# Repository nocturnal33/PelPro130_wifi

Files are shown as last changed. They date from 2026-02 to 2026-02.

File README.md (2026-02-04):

> [!CAUTION]
> ADD AT YOUR OWN RISK! <br>
> THIS CONTROLS FIRE IN YOUR HOUSE!<br>
> IF YOU ARE NOT COMFORTABLE WITH ANY OF THIS, WALK AWAY
> I AM NOT RESPONSIBEL FOR ANY DAMAGE TO YOUR PELLET STOVE OR HOUSE.

# Add wifi to your PelPro 130
*This has only been tested on a PelPro 130*

## YOU WILL NEED TO TEST THIS BEFORE RUNNING UNATTENDED
I have had this running for months with no issues. Again, If you don't feel comfortable messing with the controls of you pellet stove - **DON'T DO IT!**

## Purpose
The purpose of this is to be able to turn on the pellet stove from anywhere in the house. Maybe it's 2am and it's getting cold in the house. Go to the IP address, login, and turn it on. You cann turn it off, adjust heat level, all from the comfort of your bed.<br>
You still have to make sure you have Pellets loaded, the burn pot is clean, etc... <br>
This project assumes you are at home, near the PelPro if something were to go wrong - you will be there to monitor the pellet stove.

## Parts: 
- EMAX Servo ES08A (x1)
- ELEGOO ESP-32 (Or similar) (x1)
- 8mm x 2mm Round Magnets (x3)
- M2 X4 Hex screws (x5)
   - For Servo (x2)
   - For ESP32 (x3)

## 3D print the parts in ABS, PETG, or ASA. Do not use PLA
- Servo Motor / ESP case
- Servo Spur gear
- PelPro Gear

## Flash ESP32
- Use your IP Address / Subnet / DNS
- Create your password or omit it if needed

## Solder or connect servo wires to ESP32
- SERVO  -  RED    -  3.3v
- SERVO  -  BROWN  -  Ground
- SERVO  -  ORANGE -  GPIO18

After 3D printing parts - super glue magnets in enclosure, screw in the ESP32 using M2 screws, screw in the Servo using M2 screws.

1. Remove the knob on the PelPro 130 and replace with printed gear. Use a little sticky tack to make sure it does not come off.
2. Attach the magnetic base to the pellet stove
3. Attach the spur gear to the servo
4. Align the gears
5. With the Pellet stove OFF, go to the IP Address and test the alignment
6. Go to the IP address you selected in the .ino file and enter the password you chose
7. Test
8. Turn ON the pellet stove and enjoy

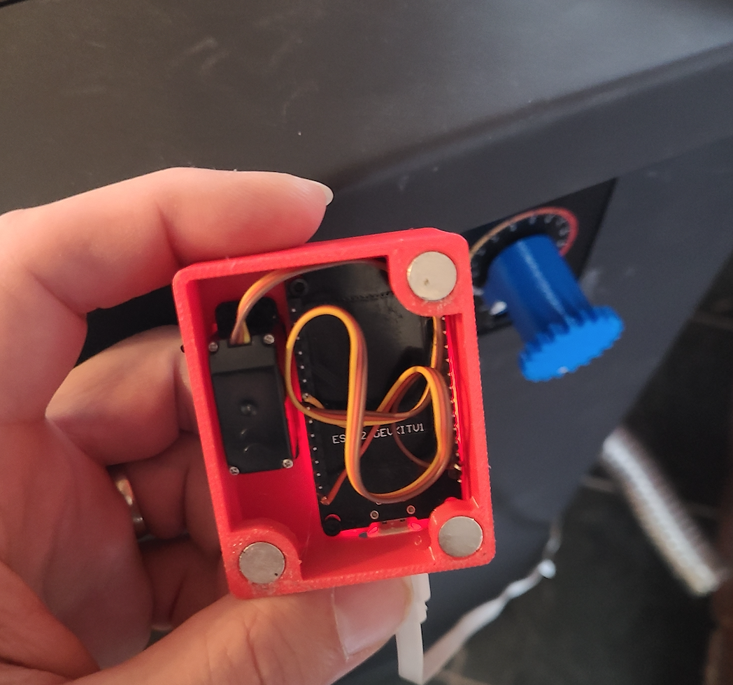
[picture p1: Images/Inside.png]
Inside of enclosure

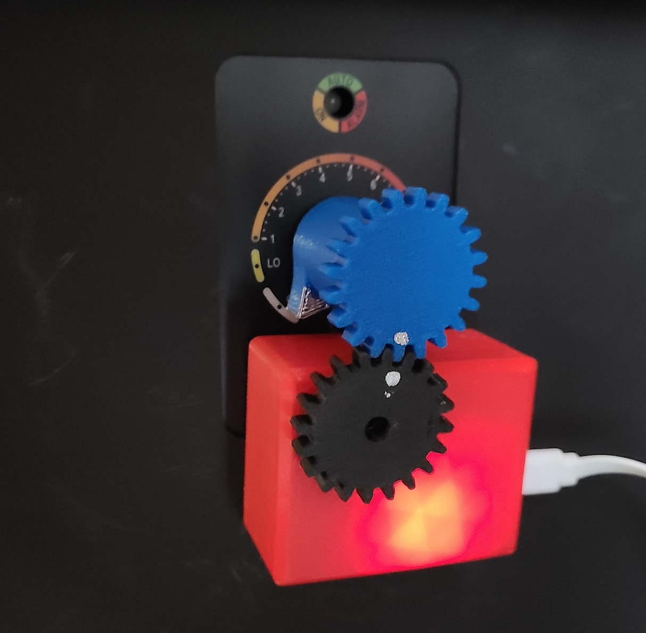
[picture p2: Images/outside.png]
Front of enclosure


## Manually adjusting heat on the PP130
Now that the servo is attached to the pellet stove, it will be harder to manually turn on the pellet stove. Keep an old phone or tablet near the PelPro 130 and use that instead of manually adjusting, or, because it is magnetically attached, move it away from the spur gear and adjust.

## Home Assistant.
This works great with Home Assistant. I am using my Google Nest to check the inside temperature and turn on the Pellet Stove based on the min and turn off on the max. Lots of ways to do this, but this works for my setup.  
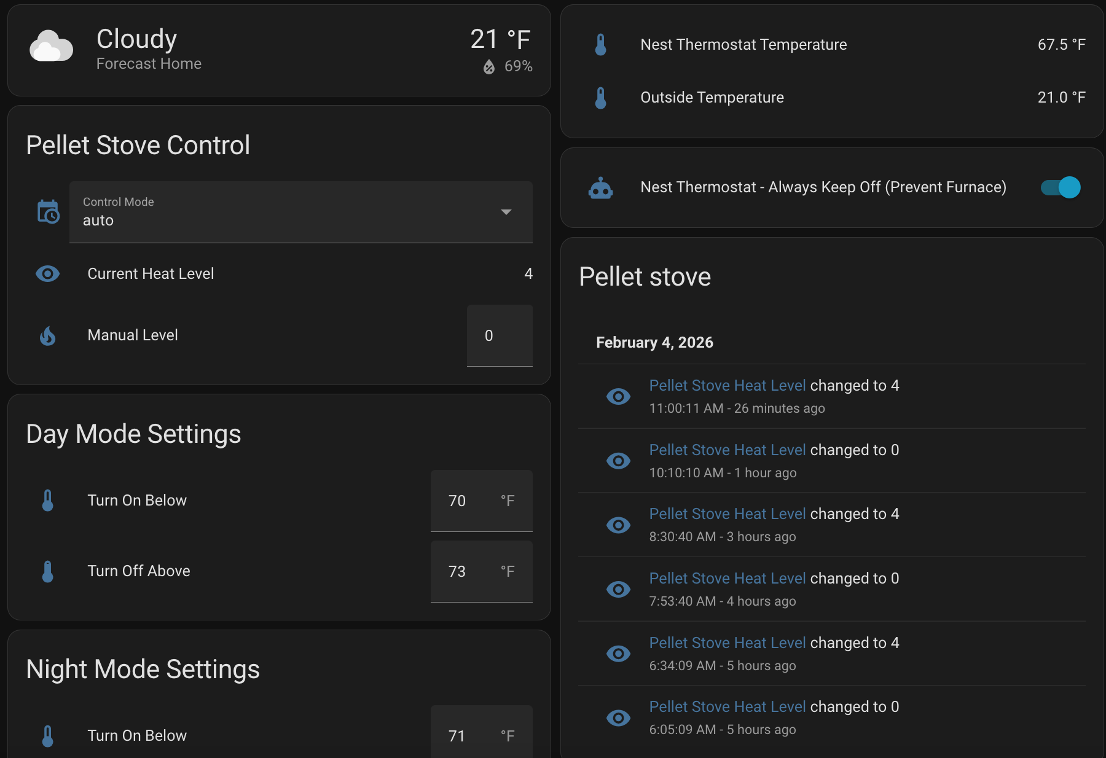
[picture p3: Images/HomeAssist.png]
Home Assistant


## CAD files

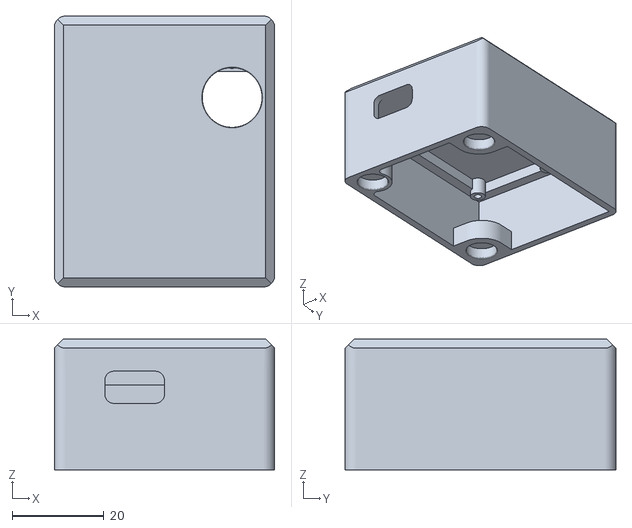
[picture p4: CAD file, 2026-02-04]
3D-Models/PelPro-Wifi-Enclosure.stl
48.0 x 59.0 x 28.5

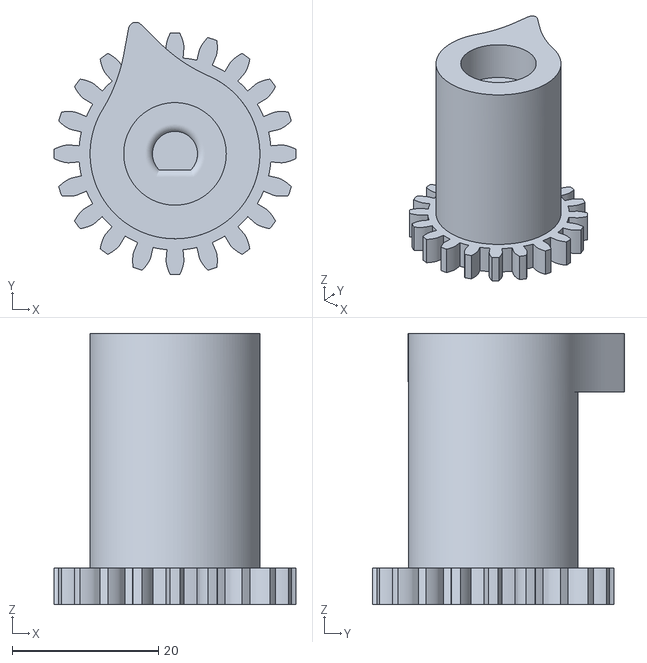
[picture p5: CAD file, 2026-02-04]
3D-Models/PelPro130-SpurGear.stl
33.0 x 34.5 x 37.0

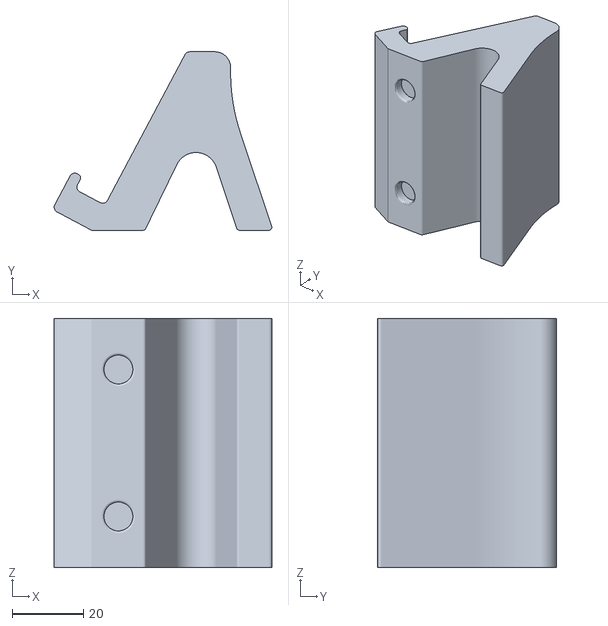
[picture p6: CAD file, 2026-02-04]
3D-Models/PhoneStand.stl
61.2 x 50.2 x 70.0

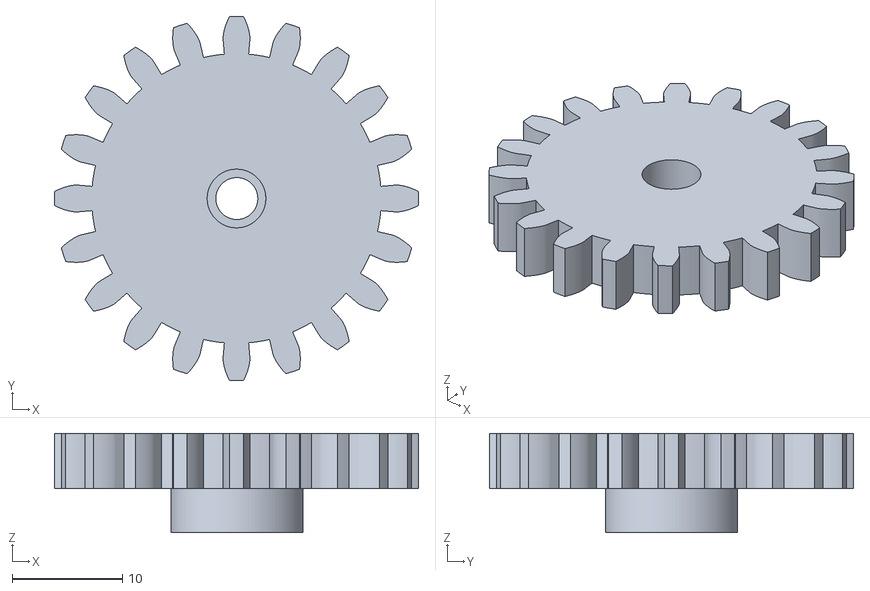
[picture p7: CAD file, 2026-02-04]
3D-Models/ServoSpurGear.stl
33.0 x 33.0 x 9.00

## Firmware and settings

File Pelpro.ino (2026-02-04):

#include <WiFi.h>
#include <WebServer.h>
#include <ESP32Servo.h>

// WiFi credentials
const char* ssid = "";
const char* password = "";

// Static IP configuration
// (Make sure to fill these in with your specific network details)
IPAddress local_IP(192, 168, 1, 200); // Change this IP to a static IP on your network
IPAddress gateway(192, 168, 1, 1);    // Use your Local IP gateway - or leave blank to keep on LAN mode
IPAddress subnet(255, 255, 255, 0);
IPAddress primaryDNS(8, 8, 8, 8);  
IPAddress secondaryDNS(8, 8, 4, 4);

// Servo setup
Servo myServo;
const int servoPin = 18;

// LED setup
const int ledPin = 2; // Built-in LED on GPIO2
unsigned long lastLedBlink = 0;
bool ledState = false;

// Web server on port 80
WebServer server(80);

// Current Heat level (0-8)
int HeatLevel = 0;

// Control LED and Servo based on WiFi status
void updateWiFiLED() {
  static wl_status_t lastWifiStatus = WL_IDLE_STATUS;
  wl_status_t wifiStatus = WiFi.status();
  unsigned long currentTime = millis();
  
  // Check if WiFi was just disconnected
  if (lastWifiStatus == WL_CONNECTED && wifiStatus != WL_CONNECTED) {
    // WiFi just disconnected
    // REMOVED: myServo.write(0) and HeatLevel = 0
    Serial.println("WiFi disconnected - Maintaining current Heat Level");
  }
  
  lastWifiStatus = wifiStatus;
  
  switch (wifiStatus) {
    case WL_CONNECTED:
      // Solid LED when connected (active-low LED usually, usually LOW is ON for built-in)
      // If your LED is off when connected, swap LOW/HIGH here
      digitalWrite(ledPin, LOW); 
      break;
      
    case WL_IDLE_STATUS:
    case WL_NO_SSID_AVAIL:
    case WL_SCAN_COMPLETED:
    case WL_CONNECT_FAILED:
    case WL_CONNECTION_LOST:
    case WL_DISCONNECTED:
      // Fast blink when disconnected or failed (250ms intervals)
      if (currentTime - lastLedBlink >= 250) {
        ledState = !ledState;
        digitalWrite(ledPin, ledState ? HIGH : LOW);
        lastLedBlink = currentTime;
      }
      break;
      
    default:
      // Slow blink for any other status (1 second intervals)
      if (currentTime - lastLedBlink >= 1000) {
        ledState = !ledState;
        digitalWrite(ledPin, ledState ? HIGH : LOW);
        lastLedBlink = currentTime;
      }
      break;
  }
}

// Main control page HTML (no password protection)
const char webpage[] PROGMEM = R"=====(
<!DOCTYPE html>
<html>
<head>
  <meta charset="UTF-8">
  <meta name="viewport" content="width=device-width, initial-scale=1">
  <title>Heat Control</title>
  <style>
    body {
      font-family: Arial, sans-serif;
      text-align: center;
      margin-top: 50px;
      background-color: #f0f0f0;
    }
    h1 {
      color: #333;
      font-size: 30px;
      font-weight: bold;
      margin-bottom: 20px;
    }
    .slider-container {
      margin: 30px auto;
      width: 80%;
      max-width: 500px;
    }
    .slider {
      width: 100%;
      height: 75px;
      background: #f0f0f0;
      outline: none;
      opacity: 0.7;
      transition: opacity 0.2s;
      cursor: pointer;
      -webkit-appearance: none;
      appearance: none;
      border-radius: 10px;
    }
    
    .slider::-webkit-slider-thumb {
      -webkit-appearance: none;
      appearance: none;
      width: 30px;
      height: 30px;
      background: #fff;
      cursor: pointer;
      border-radius: 50%;
      border: 3px solid #f44336;
      box-shadow: 0 2px 6px rgba(0,0,0,0.3);
    }
    
    .slider::-moz-range-thumb {
      width: 30px;
      height: 30px;
      background: #fff;
      cursor: pointer;
      border-radius: 50%;
      border: 3px solid #f44336;
      box-shadow: 0 2px 6px rgba(0,0,0,0.3);
    }
    
    .slider::-webkit-slider-track {
      height: 20px;
      background: #f44336;
      border-radius: 10px;
      border: none;
    }
    
    .slider::-webkit-slider-runnable-track {
      height: 20px;
      background: #f44336;
      border-radius: 10px;
      border: none;
    }
    
    .slider::-moz-range-track {
      height: 20px;
      background: #f44336;
      border-radius: 10px;
      border: none;
    }
    
    .slider:hover {
      opacity: 1;
    }
    .value-display {
      font-size: 48px;
      font-weight: bold;
      color: #4CAF50;
      margin: 20px;
    }
    .labels {
      display: flex;
      justify-content: space-between;
      margin-top: 20px;
      font-size: 14px;
      color: #666;
    }
    
    .labels span {
      cursor: pointer;
      padding: 5px 10px;
      border-radius: 3px;
      transition: background-color 0.2s;
    }
    
    .labels span:hover {
      background-color: rgba(244, 67, 54, 0.1);
    }
  </style>
</head>
<body>
  <h1>PelPro 130 - Heat Control</h1>
  <div class="value-display" id="HeatDisplay">0</div>
  <div class="slider-container">
    <input type="range" min="0" max="8" value="0" class="slider" id="HeatSlider">
    <div class="labels">
      <span onclick="setHeat(0)">OFF</span>
      <span onclick="setHeat(1)">1</span>
      <span onclick="setHeat(2)">2</span>
      <span onclick="setHeat(3)">3</span>
      <span onclick="setHeat(4)">4</span>
      <span onclick="setHeat(5)">5</span>
      <span onclick="setHeat(6)">6</span>
      <span onclick="setHeat(7)">7</span>
      <span onclick="setHeat(8)">8</span>
    </div>
  </div>

  <script>
    var slider = document.getElementById("HeatSlider");
    var display = document.getElementById("HeatDisplay");
    var isDragging = false; 

    slider.onmousedown = function() { isDragging = true; }
    slider.onmouseup = function() { isDragging = false; }
    slider.ontouchstart = function() { isDragging = true; }
    slider.ontouchend = function() { isDragging = false; }
    
    // Set Heat when clicking on labels
    function setHeat(level) {
      slider.value = level;
      display.innerHTML = level;
      
      var xhr = new XMLHttpRequest();
      xhr.open("GET", "/setHeat?level=" + level, true);
      xhr.send();
    }
    
    slider.oninput = function() {
      display.innerHTML = this.value;
    }
    
    slider.onchange = function() {
      var xhr = new XMLHttpRequest();
      xhr.open("GET", "/setHeat?level=" + this.value, true);
      xhr.send();
      isDragging = false;
    }

    function getHeatState() {
      // Only refresh if the user isn't actively dragging
      if (isDragging) {
        return;
      }
      
      var xhr = new XMLHttpRequest();
      xhr.onreadystatechange = function() {
        if (this.readyState == 4 && this.status == 200) {
          slider.value = this.responseText;
          display.innerHTML = this.responseText;
        }
      };
      xhr.open("GET", "/getHeat", true);
      xhr.send();
    }
    
    window.onload = getHeatState;
    setInterval(getHeatState, 10000); // 10000ms = 10 seconds
  </script>
</body>
</html>
)=====";

void handleRoot() {
  server.send(200, "text/html", webpage);
}

void handleSetHeat() {
  if (server.hasArg("level")) {
    HeatLevel = server.arg("level").toInt();
    HeatLevel = constrain(HeatLevel, 0, 8);
    
    int servoAngle = map(HeatLevel, 0, 8, 0, 180);
    myServo.write(servoAngle);
    
    Serial.print("Heat set to: ");
    Serial.print(HeatLevel);
    Serial.print(" | Servo angle: ");
    Serial.println(servoAngle);
    
    server.send(200, "text/plain", "OK");
  } else {
    server.send(400, "text/plain", "Bad Request");
  }
}

void handleGetHeat() {
  server.send(200, "text/plain", String(HeatLevel));
}

void setup() {
  Serial.begin(115200);
  
  // Initialize servo
  myServo.attach(servoPin);
  myServo.write(0); // Start at 0 on POWER UP only
  
  // Initialize LED (active-low)
  pinMode(ledPin, OUTPUT);
  digitalWrite(ledPin, HIGH); // Start with LED off (active-low)
  
  // Configure static IP
  // IMPORTANT: Ensure your specific IP addresses are entered here
  if (!WiFi.config(local_IP, gateway, subnet, primaryDNS, secondaryDNS)) {
    Serial.println("Static IP configuration failed!");
  }
  
  // Connect to WiFi
  Serial.println();
  Serial.print("Connecting to ");
  Serial.println(ssid);
  
  WiFi.begin(ssid, password);
  
  // Loop to wait for connection
  while (WiFi.status() != WL_CONNECTED) {
    delay(500);
    Serial.print(".");
  }
  
  Serial.println();
  Serial.println("WiFi connected!");
  Serial.print("IP address: ");
  Serial.println(WiFi.localIP());
  
  // Setup web server routes
  server.on("/", handleRoot);
  server.on("/setHeat", handleSetHeat);
  server.on("/getHeat", handleGetHeat);
  
  server.begin();
  Serial.println("Web server started!");
  Serial.println("No password protection - open access");
}

void loop() {
  server.handleClient();
  
  // Update LED based on WiFi status
  updateWiFiLED();
}
